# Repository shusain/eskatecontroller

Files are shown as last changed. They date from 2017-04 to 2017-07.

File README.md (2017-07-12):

# eskatecontroller

This is a repository for the Arduino code and some CAD files for making PCBs for making a transmitter and receiver
for controlling throttle on an ESC.

Corresponding Thingiverse page http://www.thingiverse.com/thing:1864536

Related part for holding the batteries onto the bottom of the board and for covering the VESC and voltage/amperage display http://www.thingiverse.com/thing:2243206

Other related part remixed VESC case
http://www.thingiverse.com/thing:2263285

Another new part for the board, made an LED headlight/tailight holder that act as risers between the trucks and the board.
https://www.thingiverse.com/thing:2397920

In the Arduino folder there are two sub-folders one for the transmitter/controller and one for the receiver that gets the signal
and sends a PWM signal to an ESC.  The code has comments to explain what the parts do but key points are the transmitter expects
to read an analog signal from a potentiometer on pin A1 and the receiver expects to write a PWM signal to digital pin 5.

The PCB in the Eagle folder and corresponding Eagle files can be used for simplifying and solidifying the connections between
the battery, Arduino and RF module.  There is a PNG in the Images folder that can be printed using a laser printer and transferred
to a copper plate then etched to make a PCB at home, there are lots of instructions online on how to do this but not included
here.  Using the Eagle files one could also export files for a professional fabrication house to make them or forgo them
entirely.

<table>
<tr>
<td style="text-align:center">
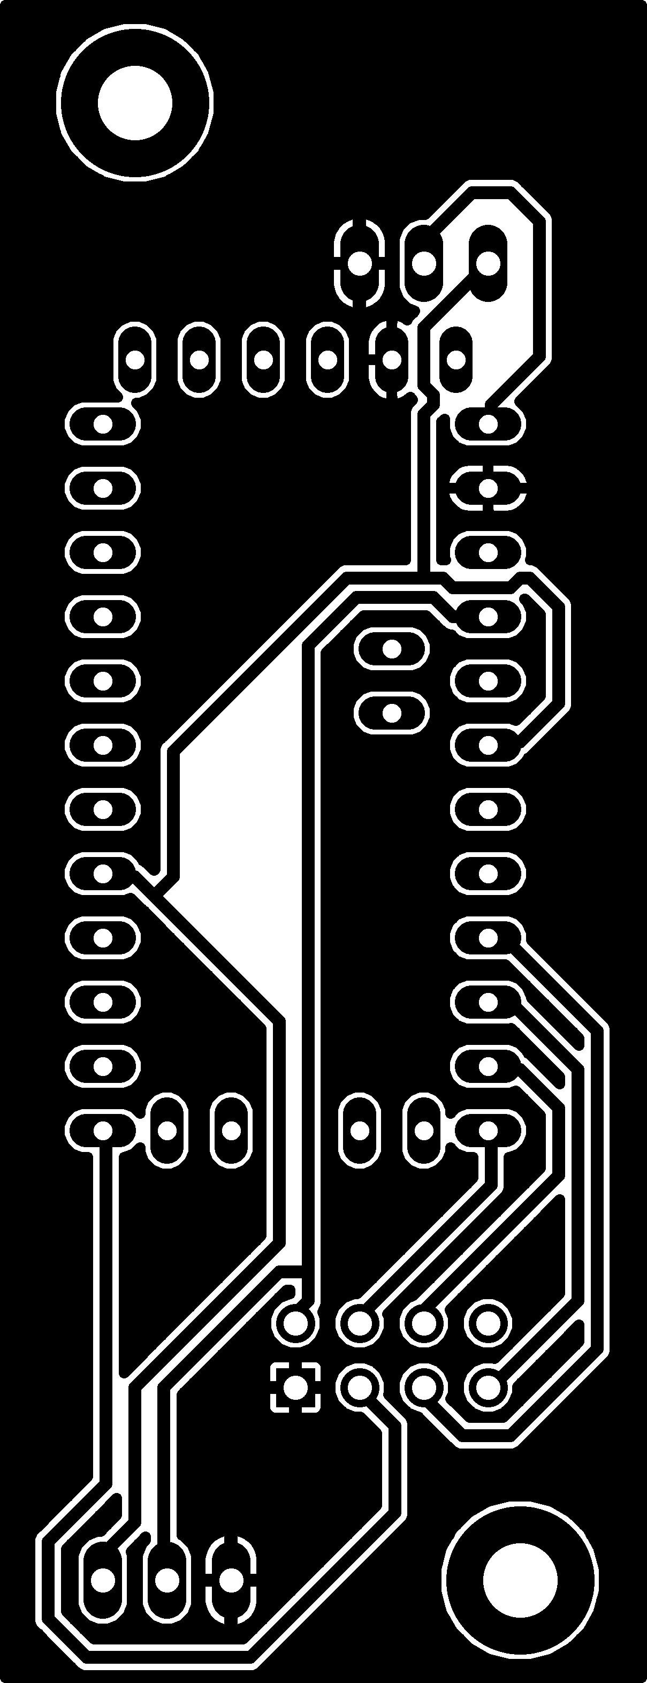
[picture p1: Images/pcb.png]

</td>
<td style="text-align:center">
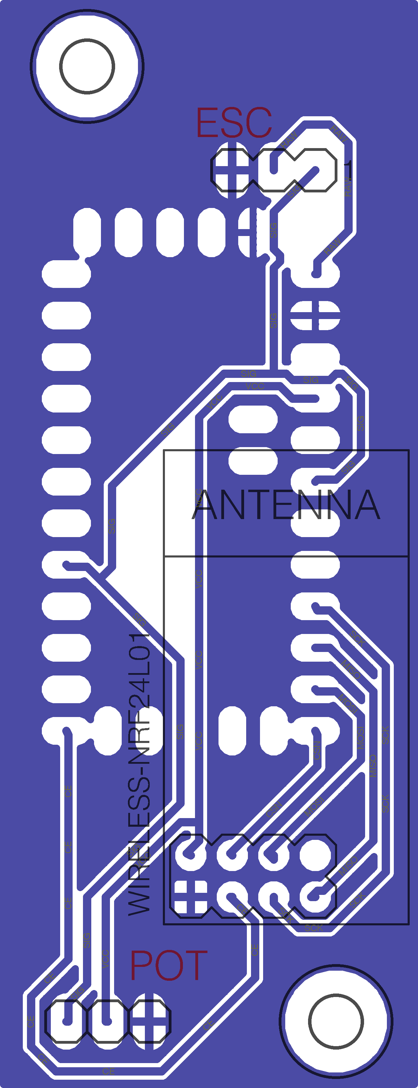
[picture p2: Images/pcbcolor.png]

</td>
</tr>
<tr>
<td>
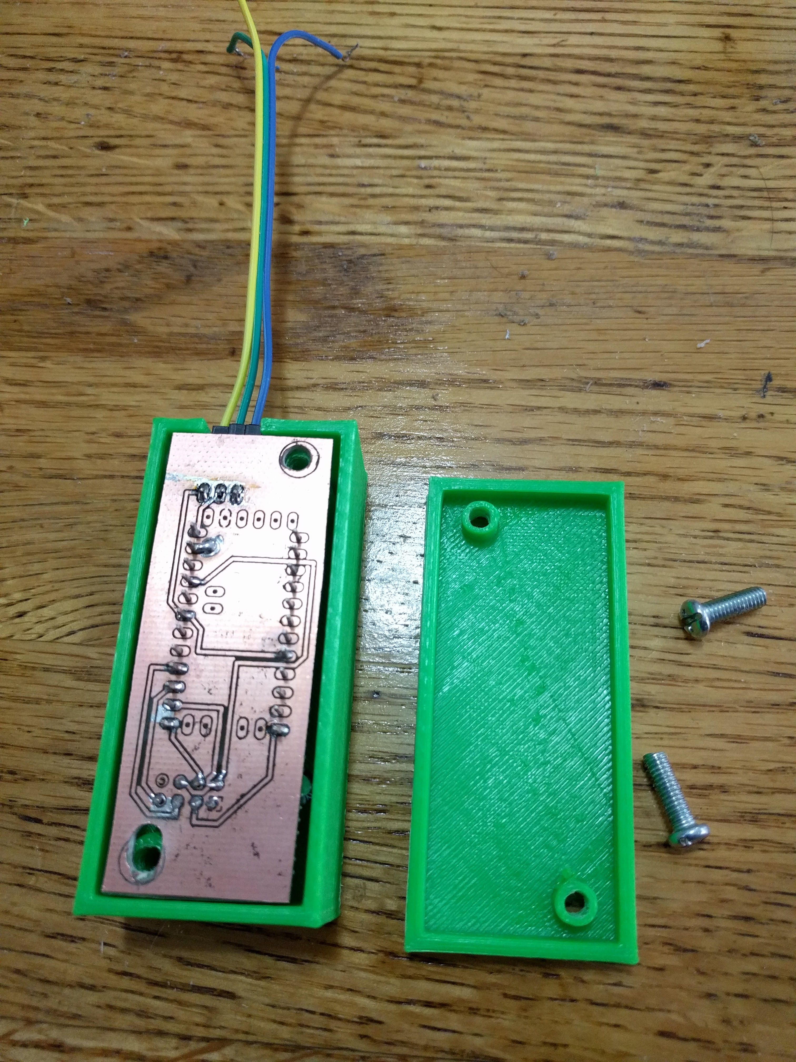
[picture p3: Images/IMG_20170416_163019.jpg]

</td>
<td>
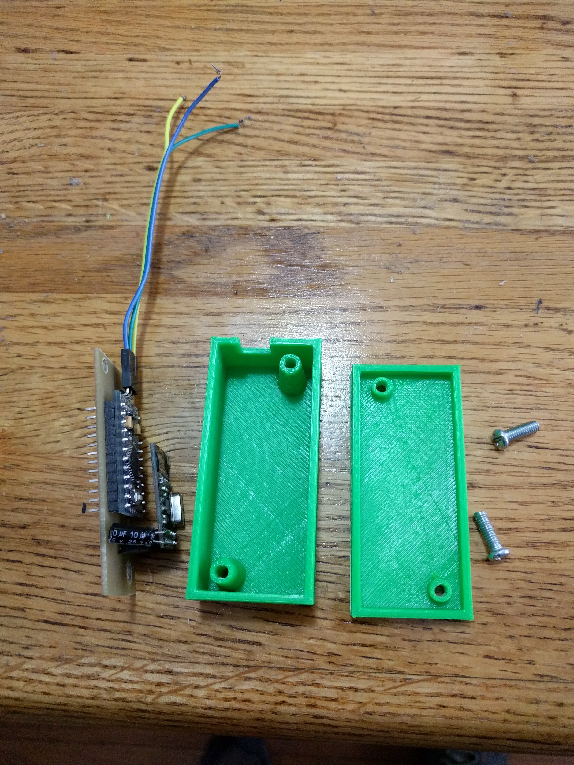
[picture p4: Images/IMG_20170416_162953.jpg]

</td>
</tr>
<tr>
<td>
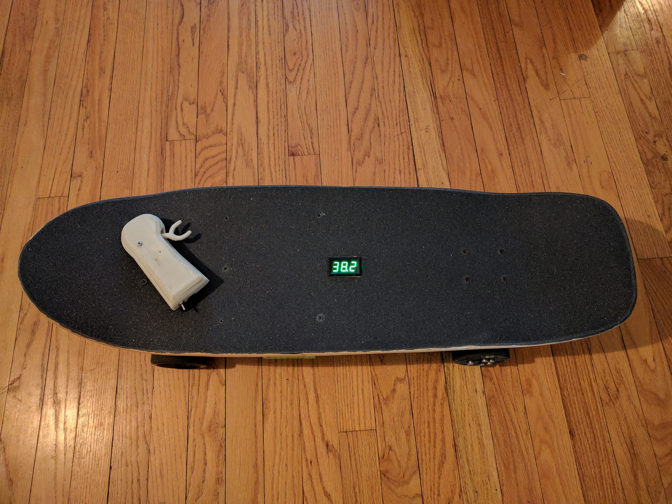
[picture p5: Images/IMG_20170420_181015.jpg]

</td>
<td>
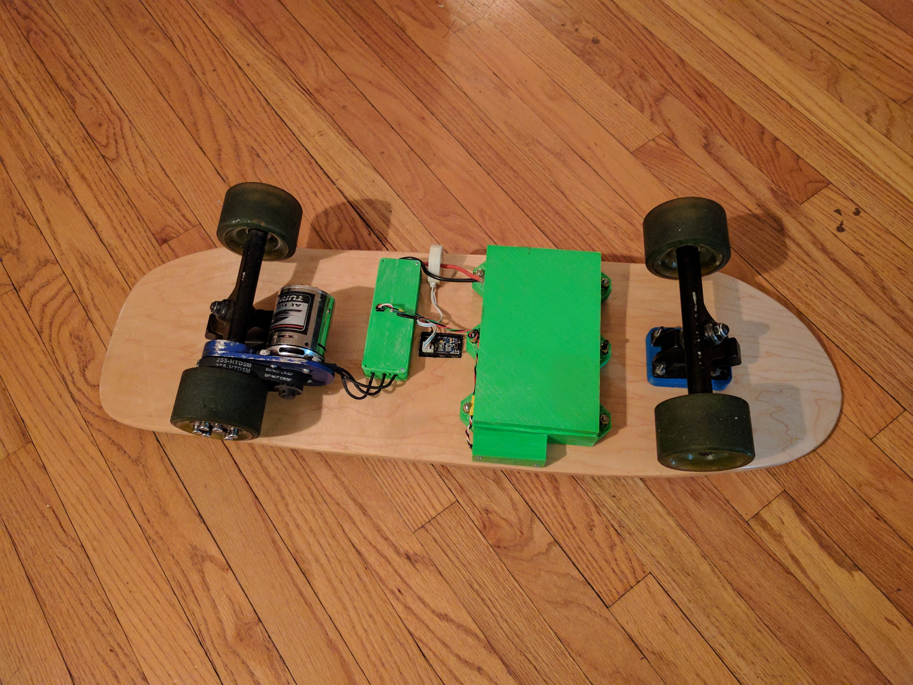
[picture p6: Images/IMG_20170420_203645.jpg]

</td>
</tr>
<tr>
<td>
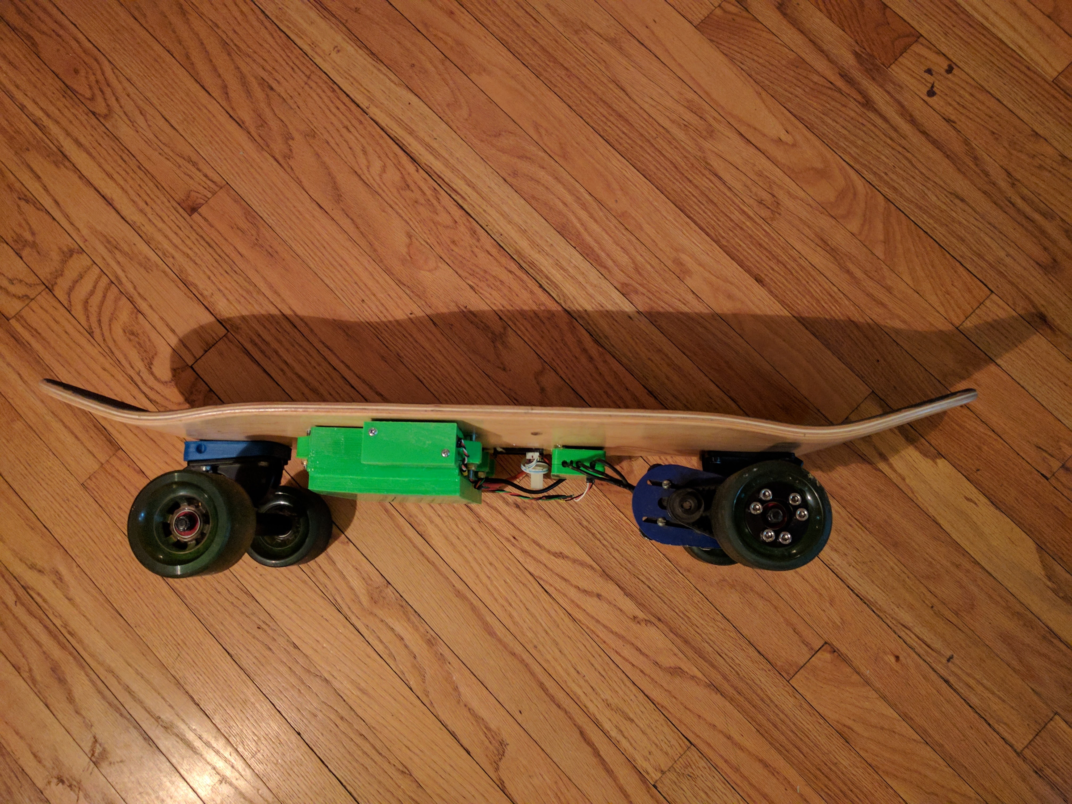
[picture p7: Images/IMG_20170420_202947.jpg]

</td>
<td>
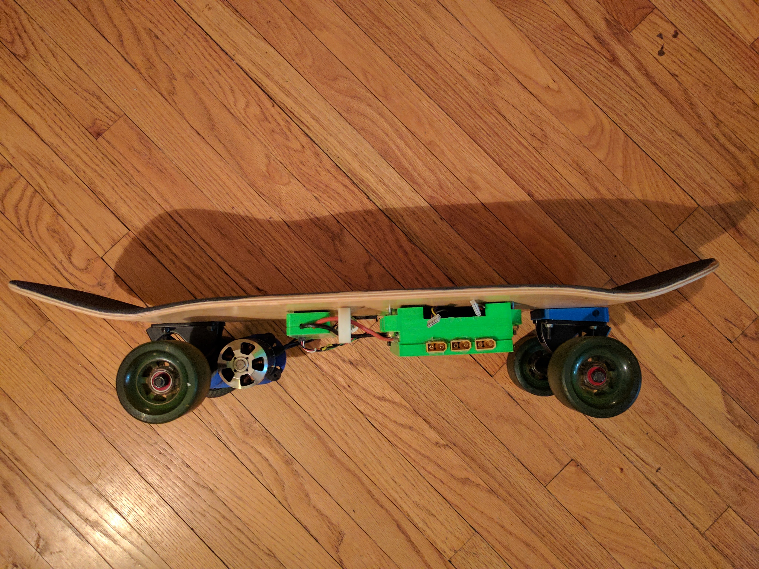
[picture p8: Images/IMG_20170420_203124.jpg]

</td>
</tr>
</table>

For the EagleCAD PCB the specific parts used are:

  - [Arduino Pro Mini 3.3V](https://www.amazon.com/Diymall-Atmega328-Atmega328p-Arduino-Esp8266/dp/B00NWF2DAU/)
  - [nRF24L01+ 2.4GHz Wireless Transceiver](https://www.amazon.com/gp/product/B00E594ZX0/)

# Assembly Overview
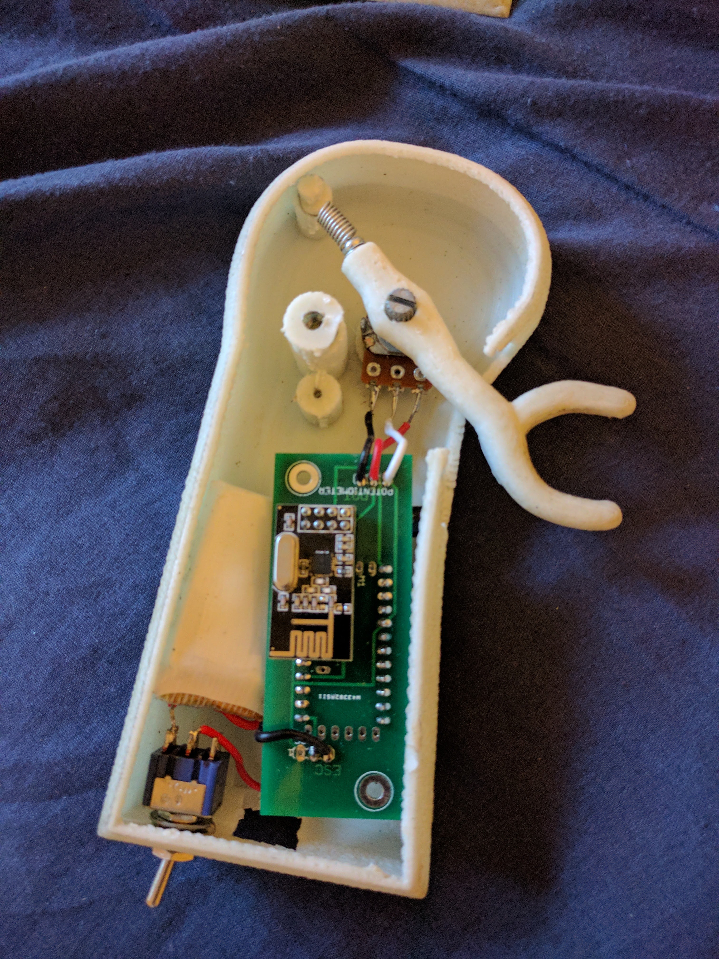
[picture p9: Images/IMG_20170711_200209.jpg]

For the PCBs made from PCBway the schematic is slightly different from what you can see from the at home PCB.  The main change is the analog pin for the potentiometer signal into the arduino was going to pin A1 before and has been moved to A2 just because I read up that some things can affect the ADC on A0 and A1 so figured I should just move it to A2 (that same line also connects to D5 which is only used on the receiver side).

There are two, three pin breakouts one marked for ESC and one marked for potentiometer.  For both of these three pin connections the ground is towards the center of the board and the power is through the middle of the three pins and the signal is the pin towards the outside edge of the board.

The ESC middle pin is power in to the RAW pin of the arduino a LiPo is enough to keep it running stable at the 8MHz speed down to below the safe level for the LiPo itself, get ones with built in cut off circuitry to avoid over discharge in the controller, cheap ones available for micro quads in 400 or 800mAh variety, have a 800 mAh one and it lasts a really long time, somewhere around 20mA of draw typically.  The POT middle pin is the 3.3V supply off the arduino.

On the controller/transmitter side you will use the ESC pins to put power into the RAW pin of the Arduino and to connect the ground (pin towards the middle).  The signal pin for the connection marked ESC won't be used in the controller.  The 3 pins for the potentiometer the middle is 3.3V from the arduino (left leg of potentiometer), the pin near the edge is the signal (middle leg of potentiometer typically), and the pin near the center of the PCB is ground (right leg of potentiometer typically). See image above.

Image below shows the way the other PCBs need to attach but in the case of the controller I actually put the arduino on the other side of the board and it is just "upside down" so the reset button and atmel chip are facing "down" at the PCB surface instead of away from it how it's pictured.  In the receiver it is done as pictured.

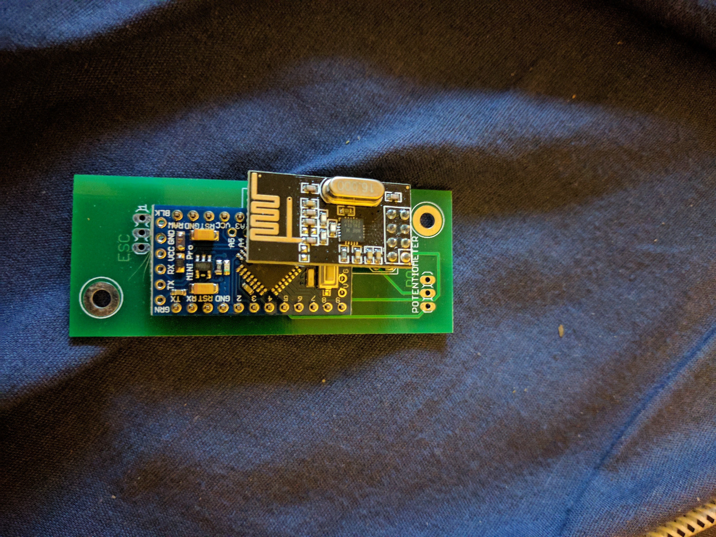
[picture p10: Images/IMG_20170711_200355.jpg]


I rearranged them in the controller just to have a little space on each side vs all the components on one side.

# Assembly Steps
Basically solder the boards together in the arrangement shown.  Good to just solder all the outside rows of arduino pins to get a nice solid connection.  If you'd like you can verify the connections based on the PCB layout below (would share the schematic but sort of useless since I just named all the nets/wires and didn't actually draw connections, it was getting too messy to deal with).

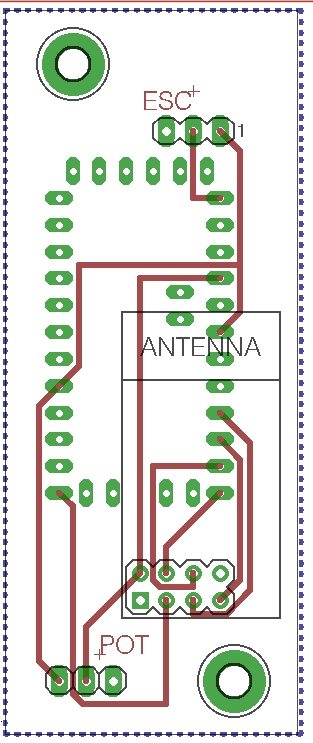
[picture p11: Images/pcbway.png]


[Note the two inside pins for the ESC and potentiometer appear to not be connected but they are connected to ground]

# Programming
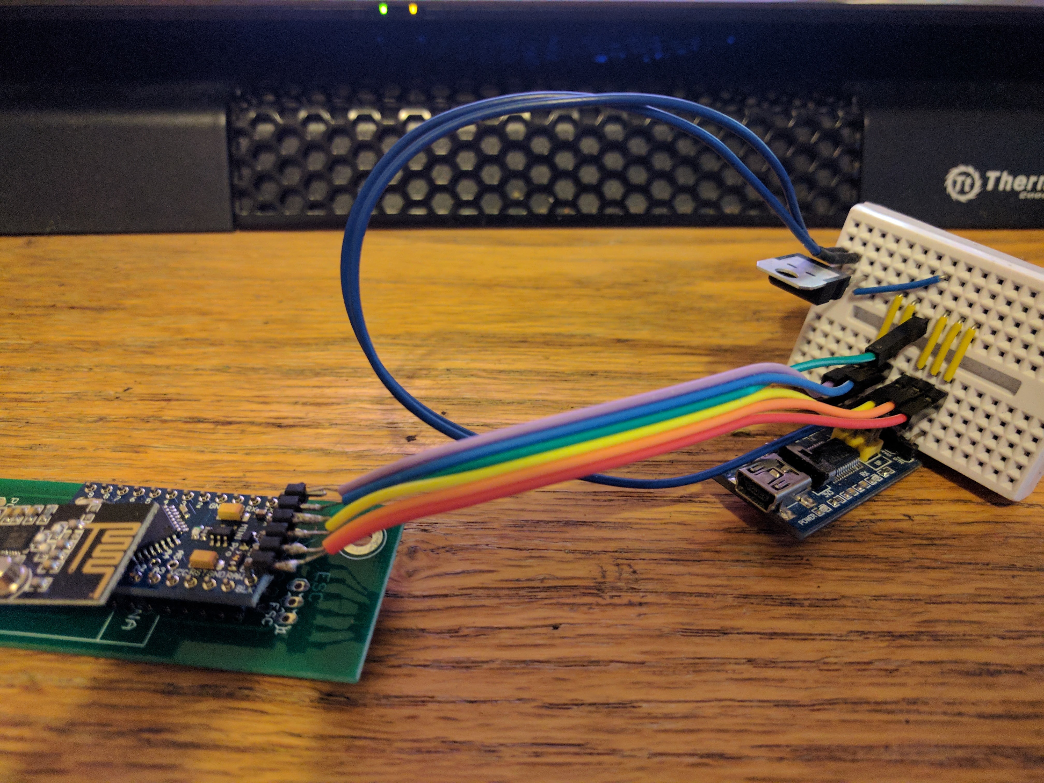
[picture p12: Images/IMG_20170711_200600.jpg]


To program the chips you'll need an FTDI breakout adapter that supports 3.3V.  Mine claimed to have 3.3V support but actually still puts 5V+ through the VCC pin and was frying the nrf chips after a few minutes of testing.  After I realized they were over voltage I started using a bench power supply or these 3.3V regulators to step down the 5V power before feeding it into the VCC for the sake of programming.

For the receiver side you can use the Arduino [project file](Arduino/rc_receiver/rc_receiver.ino) from the receiver folder without any modifications really.

For the [transmitter](Arduino/rc_controller/rc_controller.ino) side you'll need to adjust the [high/low](Arduino/rc_controller/rc_controller.ino#L19) values for the controller itself so this sort of needs to be done after assembly (when you actually know the low and high points of the potentiometer).  I had previously programmed it to get that input on startup by swinging it high and low and using those as min and max, but that seems less reliable in the long term and can lead to spinning out your motors when the value isn't set.  Anyhow long story short once assembled you will need to upload the code for the transmitter onto the arduino and then use the serial monitor to see what actual max/min values it reports and adjust the max/min in the code.

Specific steps for programming:

1. Download and install the Arduino IDE if you haven't already.

  https://www.arduino.cc/

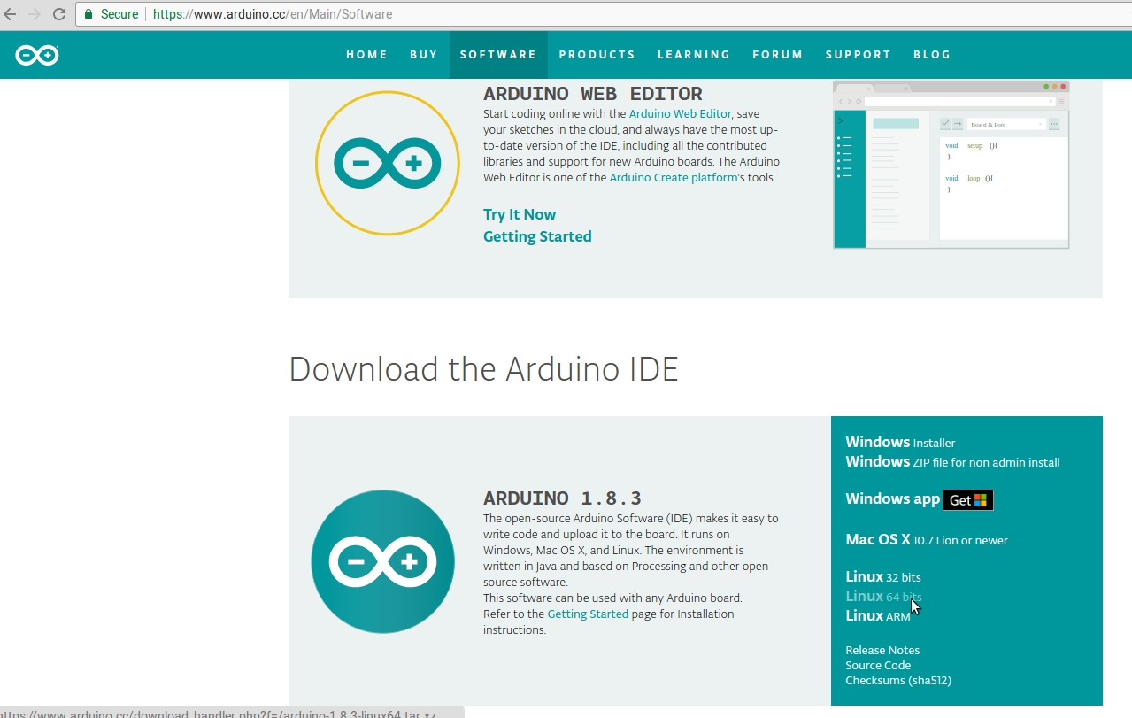
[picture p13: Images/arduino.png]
  
2. Download and extract the RF24 library into your arduino libraries folder

  https://github.com/nRF24/RF24

  Extract it to the Arduino folder (mine is in /home/shaun/Arduino/libraries/RF24) do this while the IDE is closed.
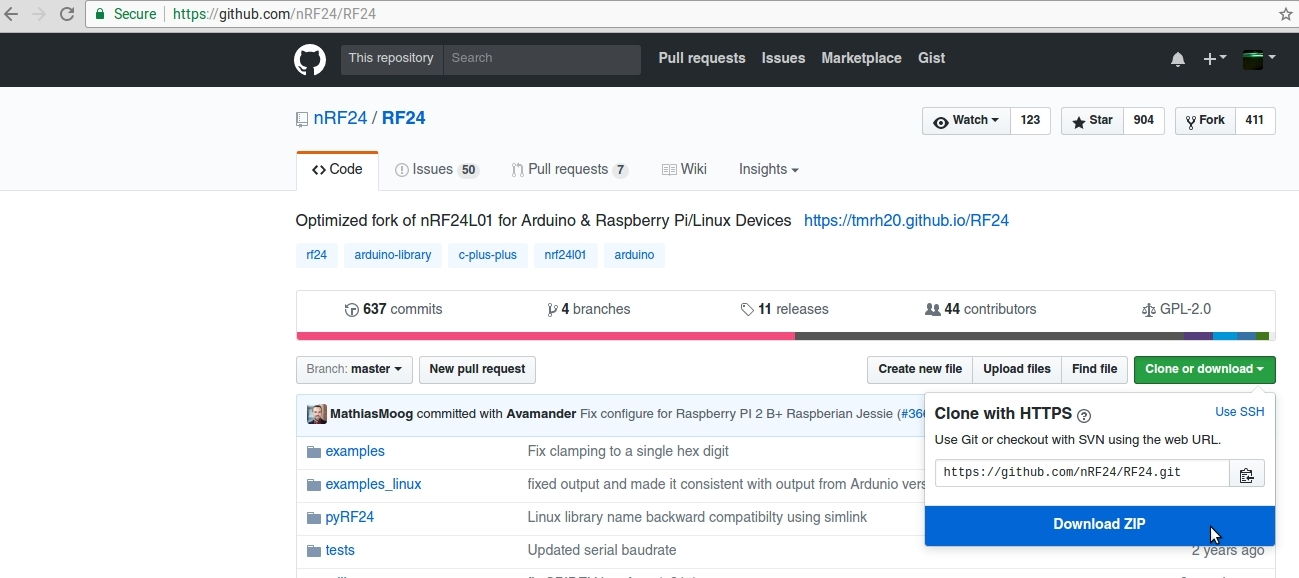
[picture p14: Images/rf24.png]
  

3.  Download and extract this repository somewhere.
4.  Open the Arduino/rc_controller/rc_controller.ino file in the Arduino IDE
5.  Change line 5 from

`//#define DEBUGMODE`

to

`#define DEBUGMODE`

This will allow it to print data to the serial line to see what the high and low values should be.

6.  Connect the controller arduino using the FTDI->USB cable to the computer
7.  Upload the code.

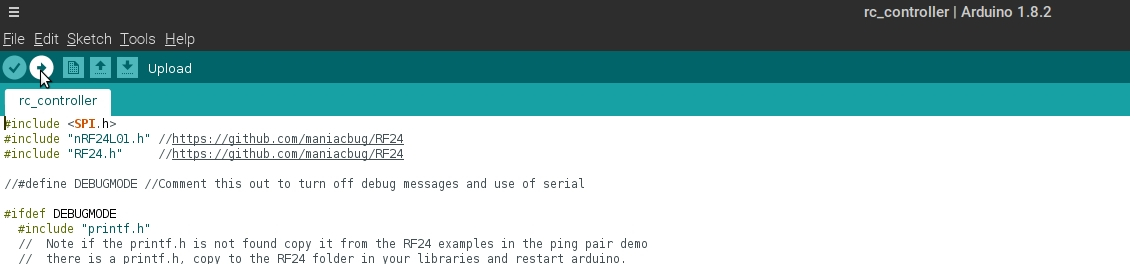
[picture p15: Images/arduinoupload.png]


8.  Check serial monitor and pull the trigger all the way to its maximum and minimum and note the values at the top and end (they will always be between 0-1024, if they go the wrong direction it doesn't really matter the value mapping will still work, but you can reverse the polarity on the potentiometer to correct that)
9.  Update the code  Lines 19 and 20 have the min and max, just set those to the values you saw and should be good to go (Arduino/rc_controller/rc_controller.ino#L19)
10. Upload the new code (can change line 66 from printing the `sensorValue` to printing the `mappedValue` so you can see that full trigger is 254, full brake is 1 and idle should be near 125).

Should be all set on the controller programming.  The ESC programming is luckily much easier, just get the boards connected, hook up the FTDI open the [receiver.ino](Arduino/rc_receiver/rc_receiver.ino), and upload the receiver code to the board.  When you connect the ESC pins on the receiver side you also won't use the POT breakout pins at all.

If you have issues or these instructions are unclear (cat stuck in toaster) let me know and will see if I can help.

---

Extra note for charging the LiPo can either use a TP4056 or just attach or keep attached the original balance lead.

---

MIT License

Copyright 2017 Shaun Husain

Permission is hereby granted, free of charge, to any person obtaining a copy of this software and associated documentation files (the "Software"), to deal in the Software without restriction, including without limitation the rights to use, copy, modify, merge, publish, distribute, sublicense, and/or sell copies of the Software, and to permit persons to whom the Software is furnished to do so, subject to the following conditions:

The above copyright notice and this permission notice shall be included in all copies or substantial portions of the Software.

THE SOFTWARE IS PROVIDED "AS IS", WITHOUT WARRANTY OF ANY KIND, EXPRESS OR IMPLIED, INCLUDING BUT NOT LIMITED TO THE WARRANTIES OF MERCHANTABILITY, FITNESS FOR A PARTICULAR PURPOSE AND NONINFRINGEMENT. IN NO EVENT SHALL THE AUTHORS OR COPYRIGHT HOLDERS BE LIABLE FOR ANY CLAIM, DAMAGES OR OTHER LIABILITY, WHETHER IN AN ACTION OF CONTRACT, TORT OR OTHERWISE, ARISING FROM, OUT OF OR IN CONNECTION WITH THE SOFTWARE OR THE USE OR OTHER DEALINGS IN THE SOFTWARE.

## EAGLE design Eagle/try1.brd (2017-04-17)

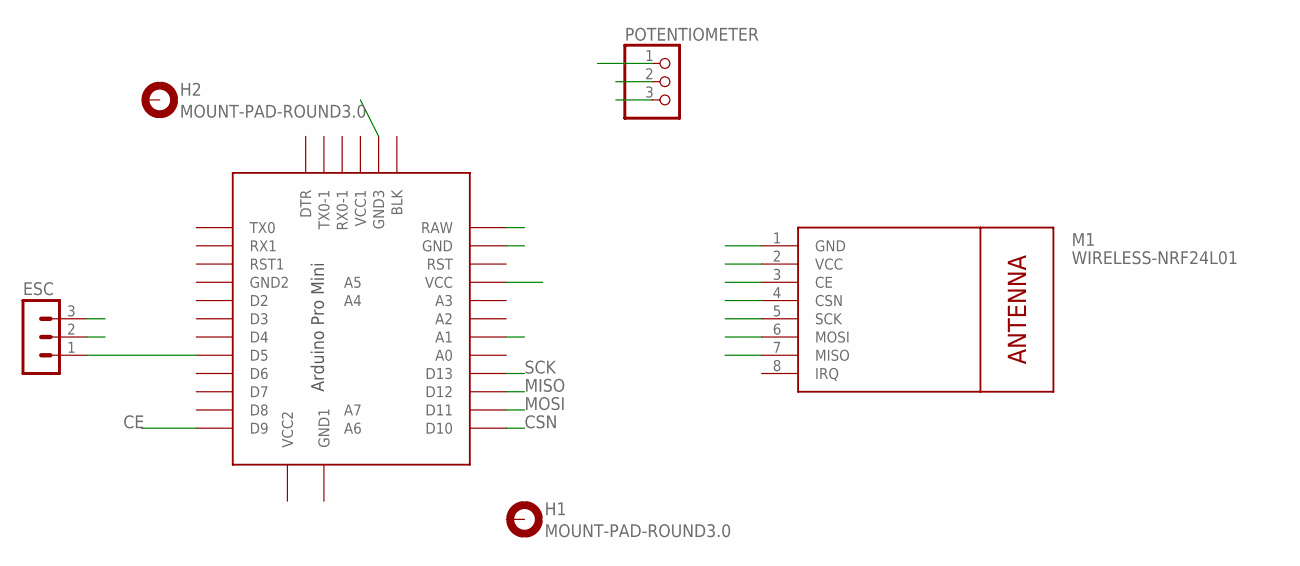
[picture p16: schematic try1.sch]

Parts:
ESC: MA03-1
H1, H2: MOUNT-PAD-ROUND3.0; 3,0-PAD
M1: WIRELESS-NRF24L01
POTENTIOMETER: PINHD-1X3; 1X03
U$2: PRO-MINI-33

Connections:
CE: M1.3 (CE), U$2.D9
CSN: M1.4 (CSN), U$2.D10
GND: ESC.3, M1.1 (GND), POTENTIOMETER.3, U$2.GND, U$2.GND3
MISO: M1.7 (MISO), U$2.D12
MOSI: M1.6 (MOSI), U$2.D11
RAW: ESC.2, U$2.RAW
SCK: M1.5 (SCK), U$2.D13
SIG: ESC.1, POTENTIOMETER.1, U$2.A1, U$2.D5
VCC: M1.2 (VCC), POTENTIOMETER.2, U$2.VCC

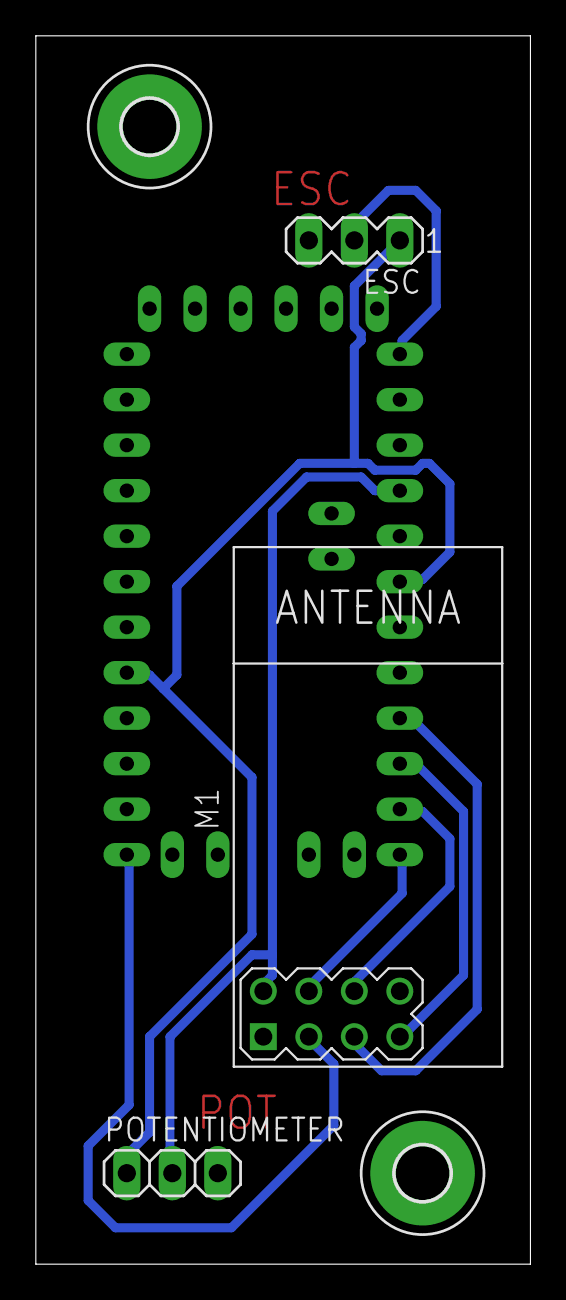
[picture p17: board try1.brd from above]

Board: 2 copper layers, 27.6 x 68.6 mm, 6 parts (0 on the bottom side), 9 nets.

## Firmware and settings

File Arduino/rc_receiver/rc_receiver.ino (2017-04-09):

#include <nRF24L01.h> //https://github.com/maniacbug/RF24
#include <RF24.h> //https://github.com/maniacbug/RF24
#include <SPI.h>
#include <elapsedMillis.h>
#include "Servo.h"

#define DEBUGMODE //Comment this out to turn off debug messages and use of serial

#ifdef DEBUGMODE
#include <printf.h>     //uncomment for debug info
#endif

//Millisconds that can occur between received packets before an idle signal is sent to ESC
const int TIMEOUT_AND_IDLE = 1000;

//Microseconds to pulse high for pwm signal to ESC
const int ESC_MIN = 1500;
const int ESC_MAX = 2000;
const int ESC_IDLE = 1750;

#ifdef DEBUGMODE
//Just used to give some basic live debug info, stays high when getting bad signals
const int LED1 = 13;
#endif

//Used to write PWM signals to the ESC (has writeMicroseconds method for setting a pwm signal)
Servo myServo; 

//Used to keep track of how long it has been since receiving a signal, sends idle on servo if greater than 1 second
elapsedMillis timeElapsed;

//nrf module related constants and variables below
//Chip enable pin
const int CE_PIN = 9;
//Chip select pin
const int CS_PIN = 10;

// Radio object for receiving data
RF24 radio(CE_PIN, CS_PIN);

//Pipe matches pipe in transmitter
const uint64_t PIPE = 0xE8E8F0F0E1LL;
uint8_t PIPE_NUM =1;

// Buffer for reading in the payload sent by the transmitter/controller
int msg[1]; 


void setup(void){
  radio.begin();
  radio.setPALevel(RF24_PA_LOW);
  radio.setDataRate(RF24_250KBPS);
  radio.setChannel(108);
  radio.openReadingPipe(PIPE_NUM,PIPE);
  radio.startListening();
  pinMode(5, OUTPUT);

  myServo.attach(5);
  myServo.writeMicroseconds(ESC_IDLE);
  
  #ifdef DEBUGMODE
  Serial.begin(9600);
  pinMode(LED1, OUTPUT);
  printf_begin();
  #endif
}
void loop(void){
  
  if (radio.available(&PIPE_NUM)){
  
    #ifdef DEBUGMODE 
    radio.printDetails();
    #endif
    
    bool done = false;
    while (!done){
      done = radio.read(msg, 1);
      if (msg[0] <= 0 || msg[0] > 254){
        #ifdef DEBUGMODE
        Serial.println("Bad signal received");
        digitalWrite(LED1, HIGH);
        #endif
        
      } else {
        // Translates value sent over wifi to microseconds in range for ESC
        int msgInMicroSeconds = map(msg[0],1,254, ESC_MIN, ESC_MAX);
        myServo.writeMicroseconds(msgInMicroSeconds);
        timeElapsed = 0;
        
        #ifdef DEBUGMODE
        digitalWrite(LED1, LOW);
        Serial.println(msg[0]);
        #endif
      }
    }
  }
  // If no message was received and a second has passed put the ESC in neutral
  if(timeElapsed > TIMEOUT_AND_IDLE){
    
    myServo.writeMicroseconds(ESC_IDLE);
    
    #ifdef DEBUGMODE
    Serial.println("frack, we've lost signal captain");
    radio.printDetails();
    #endif
  }
  delay(10);
}

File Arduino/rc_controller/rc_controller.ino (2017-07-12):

#include <SPI.h>
#include "nRF24L01.h" //https://github.com/maniacbug/RF24
#include "RF24.h"     //https://github.com/maniacbug/RF24

//#define DEBUGMODE //Comment this out to turn off debug messages and use of serial

#ifdef DEBUGMODE
  #include "printf.h"
  //  Note if the printf.h is not found copy it from the RF24 examples in the ping pair demo
  //  there is a printf.h, copy to the RF24 folder in your libraries and restart arduino.
#endif

//These values are used to keep track of bounds of the analog input
//the values are translated into a range of 1-255 to transmit to the
//receiver, on that side it will map the value to 1500-2000 micro seconds
//for the ESC

//*** ADJUST THESE FOR YOUR CONTROLLER ***//
int max = 621;
int min = 458;

// Everything below here can remain the same assuming you use analog pin 1 and standard pin layout for the rf module
// https://arduino-info.wikispaces.com/Nrf24L01-2.4GHz-HowTo See "Arduino pin for RF24 Library"

int msg[1];                             //Stores 1 byte message payload
RF24 radio(9, 10);                      //Creates the radio object for config and tranmission
const uint64_t pipe = 0xE8E8F0F0E1LL;   //ID for the connection
int SW1 = 7;

int sensorPin = A2;    // select the input pin for the potentiometer
int sensorValue = 0;  // variable to store the value coming from the sensor


void setup() {
  pinMode(A1, INPUT);

  //Start up and setup the radio configuration
  //TODO: there are lots of forks of this library see which one appears most active consider switching.
  radio.begin();
  radio.setPALevel(RF24_PA_LOW);    //Set power level, lower consumes less power but is more easily obstructed
  radio.openWritingPipe(pipe);      //Controller only transmits for the time being so we open a connection to send data
  radio.setDataRate(RF24_250KBPS);  //Using a relatively low data rate, should have a bit better reliability and is sufficient for small payload
  radio.setChannel(0);            //Uses the last possible channel on the nrf module


#ifdef DEBUGMODE
   Serial.begin(9600);  //uncomment for debugging
   printf_begin();      //uncomment for debugging
#endif
}

void loop() {
  // read the value from the sensor:
  sensorValue = analogRead(sensorPin);

  //Map value from 1 to 255 (skipping 0 since receiver seems to see that as bad data), was 10-bit from analog read mapping to 8-bit
  //to fit in the payload as a single byte.
  int mappedValue = map(sensorValue, min, max, 1, 254);
  if (mappedValue < 1)
    mappedValue = 1;
  if (mappedValue > 254)
    mappedValue = 254;

#ifdef DEBUGMODE
  //radio.printDetails();
  Serial.println(sensorValue);
#endif

  msg[0] = mappedValue;
  radio.write(msg, 1); //Message is in the bottle
}

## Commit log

2016-12-15 Initial Commit Arduino files and Eagle 7.7.0 files
    [try1.brd, try1.sch]
2017-04-09 Fixing so values above 254 are ignored using specific channel for listening.
    Had an issue when the MOSI pin 6 on the nrf module came loose and the receiver goes full throttle, changing to full throttle being 254 so can detect the 255 bad signals if the MOSI pin comes disconnected to avoid run aways.
    [rc_receiver.ino]
2017-04-09 Updating to go from 1 to 254
    Excluding 0 and 255 since these can both come from the radio when there is no signal received (loose connections)
    [rc_controller.ino]
2017-04-15 Updating the PCB design
    Changed the design to fit better in a controller and have a servo style plug so the ground and power can't be reversed only the ground and signal can be reversed which won't damage the circuit. Also added a ground plane and space for drilling holes for M3 screws.
2017-04-15 Adding some real photos of the PCB print
    Note there is a blob to connect the ground but this has been corrected in the png exported just wasn't corrected before I etched the board.
2017-04-15 Added 3 pins for potentiometer
    Added another 3 pin connector for the potentiometer to be wired to in the controller/transmitter side. Currently both signals (transmitter or receiver) are on the same line but only one will ever be used at a given time anyway so shouldn't pose any issue. Redid the routing still seems pretty clean. Time to make a box for this thing.
2017-04-16 Updating image paths to show the laser print version and full color version.
2017-04-17 Just cleaning up and updating the eagle files.
    [try1.brd, try1.sch]
2017-04-17 Added image of final PCB in receiver box
2017-04-21 Added some more images and upped the power output on the remote to overcome any interference.
    [rc_controller.ino]
2017-04-21 Added one more picture of the PCB itself from a side view
2017-07-12 Updates to the controller code for the new PCBs.
2017-07-12 Updates based on PCBway boards.
2017-07-12 extra note on charging

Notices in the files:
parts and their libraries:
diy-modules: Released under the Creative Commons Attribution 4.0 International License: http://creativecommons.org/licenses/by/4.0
